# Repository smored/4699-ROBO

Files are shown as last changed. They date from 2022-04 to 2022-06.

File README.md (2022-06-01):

Computer Vision Target Shooting Robot
=====================================

Objective:
----------
"The design project is to develop a robot that competes in an [arena](https://cdn.discordapp.com/attachments/817281300821049352/977007824553009233/unknown.png). The robot begins in a start box, and when driving forward breaks an IR beam to start the timer. The robot must then strike 4 contact plates and continue on to the finish box where the timer is stopped. The arena must be completed in two different modes, 1) teleoperation where the user drives via commands and images over TCP/IP and 2) autonomous mode where the robot solves the arena without human intervention."

Our Solution:
-------------
We decided to base our design around two [NEMA 17](https://www.amazon.ca/gp/product/B09N3NRTW9/ref=ppx_yo_dt_b_asin_title_o06_s01?ie=UTF8&psc=1) stepper motors using respective [L298N](https://www.amazon.ca/gp/product/B00XAGRQTO/ref=ppx_yo_dt_b_asin_title_o07_s00?ie=UTF8&psc=1) driver circuit boards and a [Teensy 4.0](https://www.amazon.ca/Teensy-4-0-with-Pins/dp/B08259KDHY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) to interface the motors to the [Raspbery Pi 4b](https://www.amazon.ca/s?k=rasberry+pi+4+b&crid=1HV9MO5X30TG&sprefix=rasb%2Caps%2C238&ref=nb_sb_ss_ts-doa-p_1_4). We would use two [ultrasonic sensors](https://www.sparkfun.com/products/15569) for positional alignment, a [servo](https://www.amazon.ca/gp/product/B07VJG5QTJ/ref=ppx_yo_dt_b_asin_title_o05_s00?ie=UTF8&psc=1) for turret aiming, a [servo](https://www.amazon.ca/gp/product/B07KR24YX8/ref=ppx_yo_dt_b_asin_title_o03_s00?ie=UTF8&psc=1) for firing at the targets, and finally a [pi camera](https://www.amazon.ca/Keyestudio-Camera-Module-5MP-Raspberry/dp/B073RCXGQS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). We decided to split the main functionality of the robot into two parts: Driving (Teensy) and Detection (Raspberry Pi). There are two main reasons for this decision, first we wanted to unload as much possible processing from the raspberry pi so that our computer vision algorithm could run faster, and second it allowed us to completely isolate our workloads into two seperate entities, and thus we could work asychronously. 

For Auto mode our algorithm was based around a state machine, each state being defined as a portion of the arena. The Teensy would drive the motors to the first location, wait for feedback from the Pi on when the target was successfully hit, then move to the second target, and so on. The Pi would grab the state of each target from a server hosted by the arena over TCP/IP, and pass that information onto the Teensy via UART. 

The method used to aim the cannon was to use the pi camera to scan for ArUCO QR codes, using that information encoded into screenspace, determine whether the target was on the left or right of the centre of the camera. If the ArUCO was in the centre, it would fire the cannon.

In manual driving mode, the user would input keypresses into a windows client on a laptop that communicated with the Pi over TCP/IP. The client additionally fetched a camera feed from the arena, and a camera feed from the Pi to enable the user to fully drive the unit without line of sight to the arena.

Media:
------
PCB pic
robot pic 1
servo pic

[More Robot](https://photos.app.goo.gl/skK17sW5vWhY1REk8)

Credits:
-------
**Kurt Querengesser**

Author of PI code and Lead Parts Designer

Kurt Querengesser (https://www.linkedin.com/in/kurt-querengesser/)

**Michael Andrews**

Author of Microcontroller Code and Lead PCB Designer

Michael Andrews (https://www.linkedin.com/in/michael-andrews-b0ab8217a/)

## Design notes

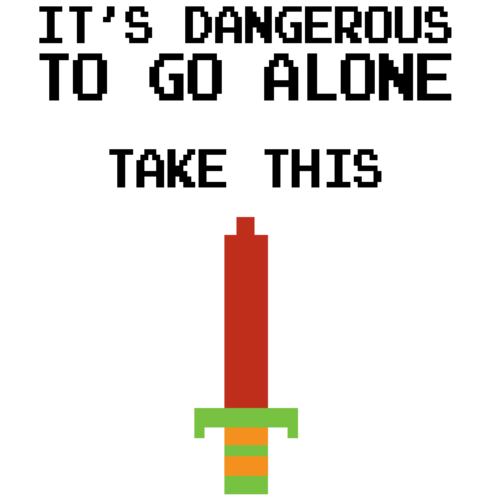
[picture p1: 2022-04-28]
KiCad PiHat/Graphics/Dangerous.png

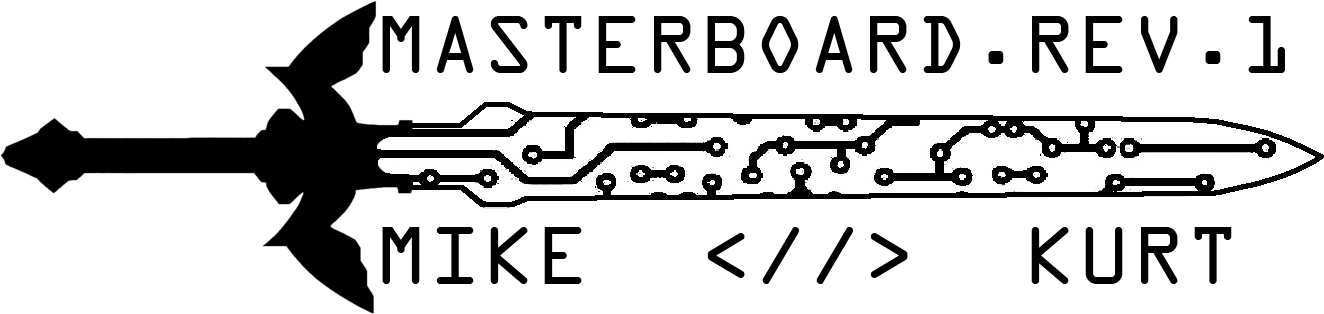
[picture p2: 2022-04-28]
KiCad PiHat/Graphics/masterboard.png

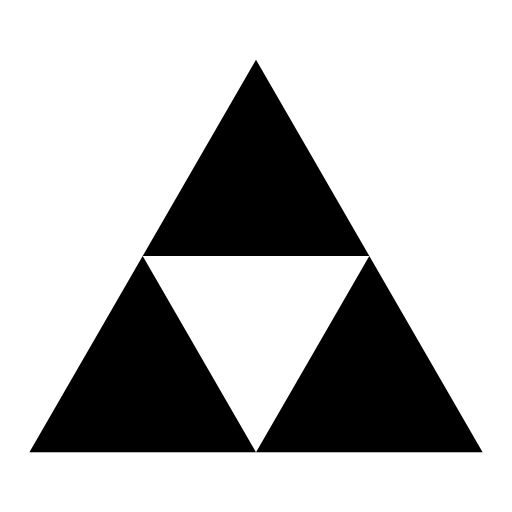
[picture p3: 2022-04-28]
KiCad PiHat/Graphics/Triforce.png

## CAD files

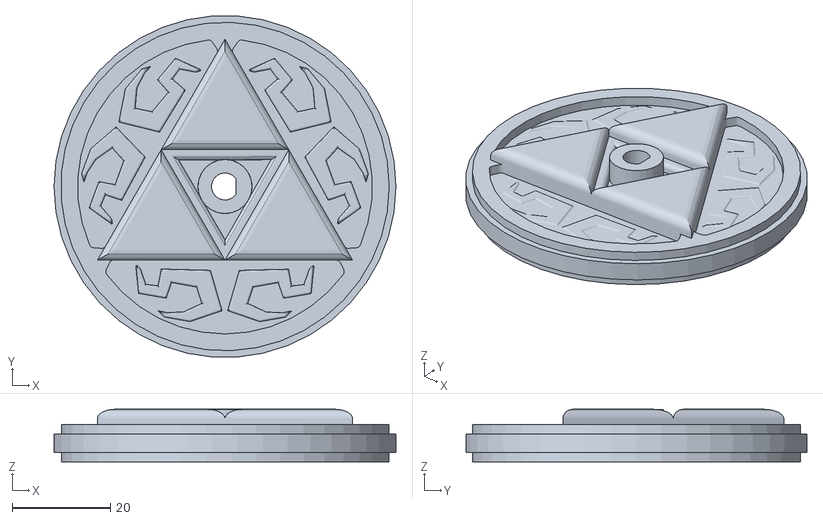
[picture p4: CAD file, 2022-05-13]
MODELS/STLs/wheel.stl
69.6 x 69.4 x 10.7

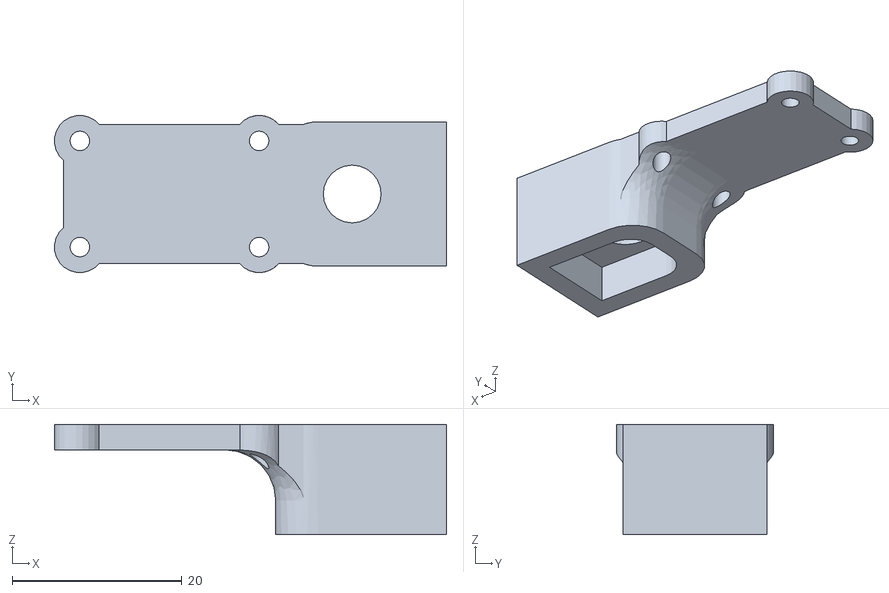
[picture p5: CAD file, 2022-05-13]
MODELS/STLs/camera_mount.stl
46.1 x 18.5 x 13.0

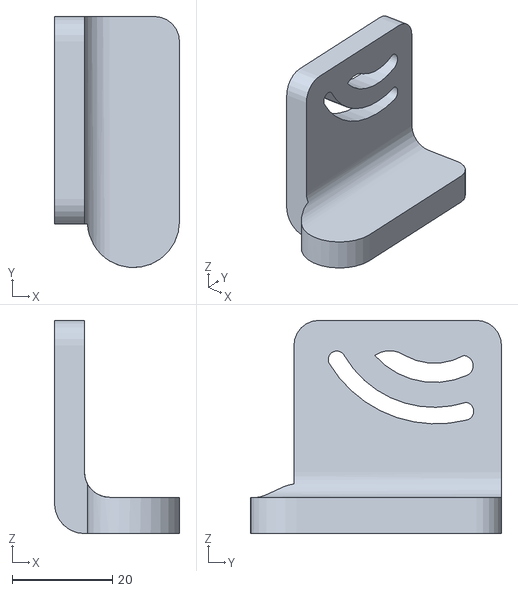
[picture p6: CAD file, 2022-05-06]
MODELS/STLs/launcher_mount.stl
24.9 x 50.0 x 42.5

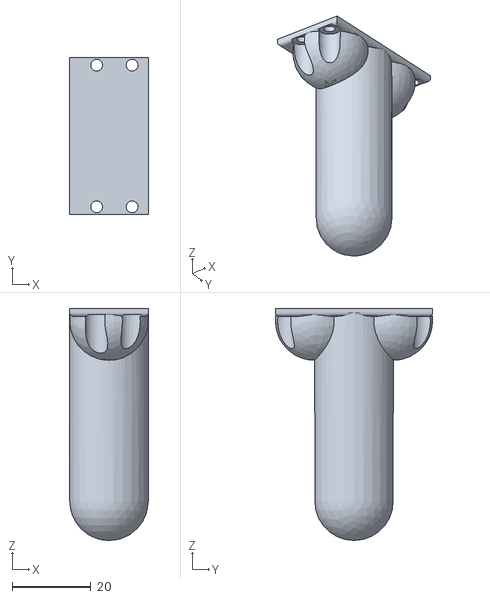
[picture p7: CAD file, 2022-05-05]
MODELS/STLs/C&B.stl
20.0 x 40.0 x 58.9

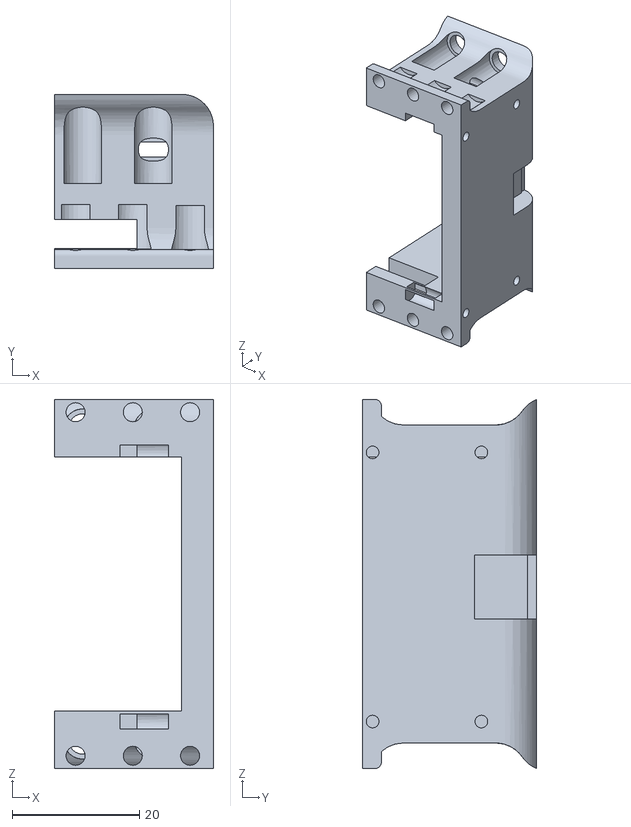
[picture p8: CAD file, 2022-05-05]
MODELS/STLs/servo_mount.stl
25.0 x 27.4 x 58.0

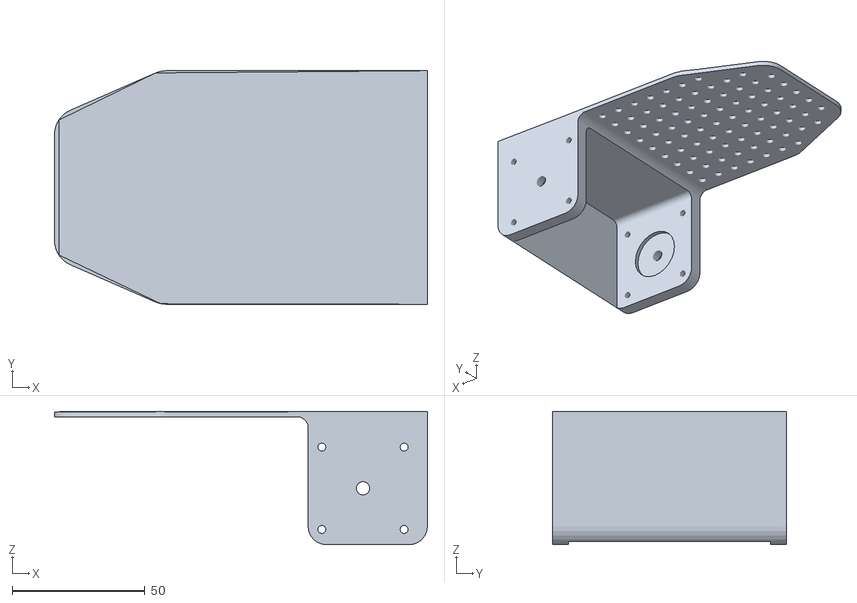
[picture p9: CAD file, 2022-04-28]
MODELS/STLs/chassis.stl
140.5 x 88.0 x 50.3

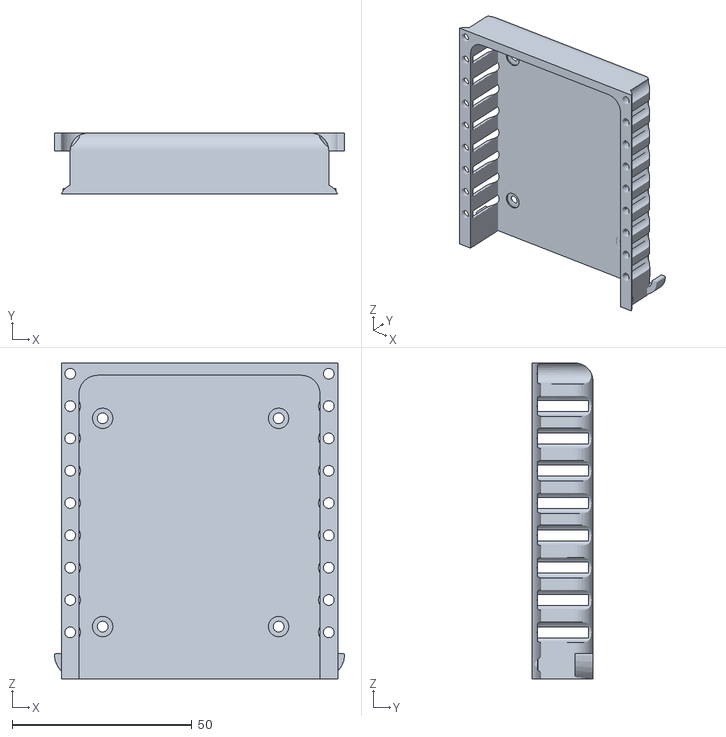
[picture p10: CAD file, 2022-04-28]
MODELS/STLs/battery_holder.stl
80.9 x 17.0 x 88.0

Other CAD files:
MODELS/CarBase.DWG
MODELS/RaspberryHatBoard.DWG
MODELS/launcher.DWG
MODELS/wheel.dwg

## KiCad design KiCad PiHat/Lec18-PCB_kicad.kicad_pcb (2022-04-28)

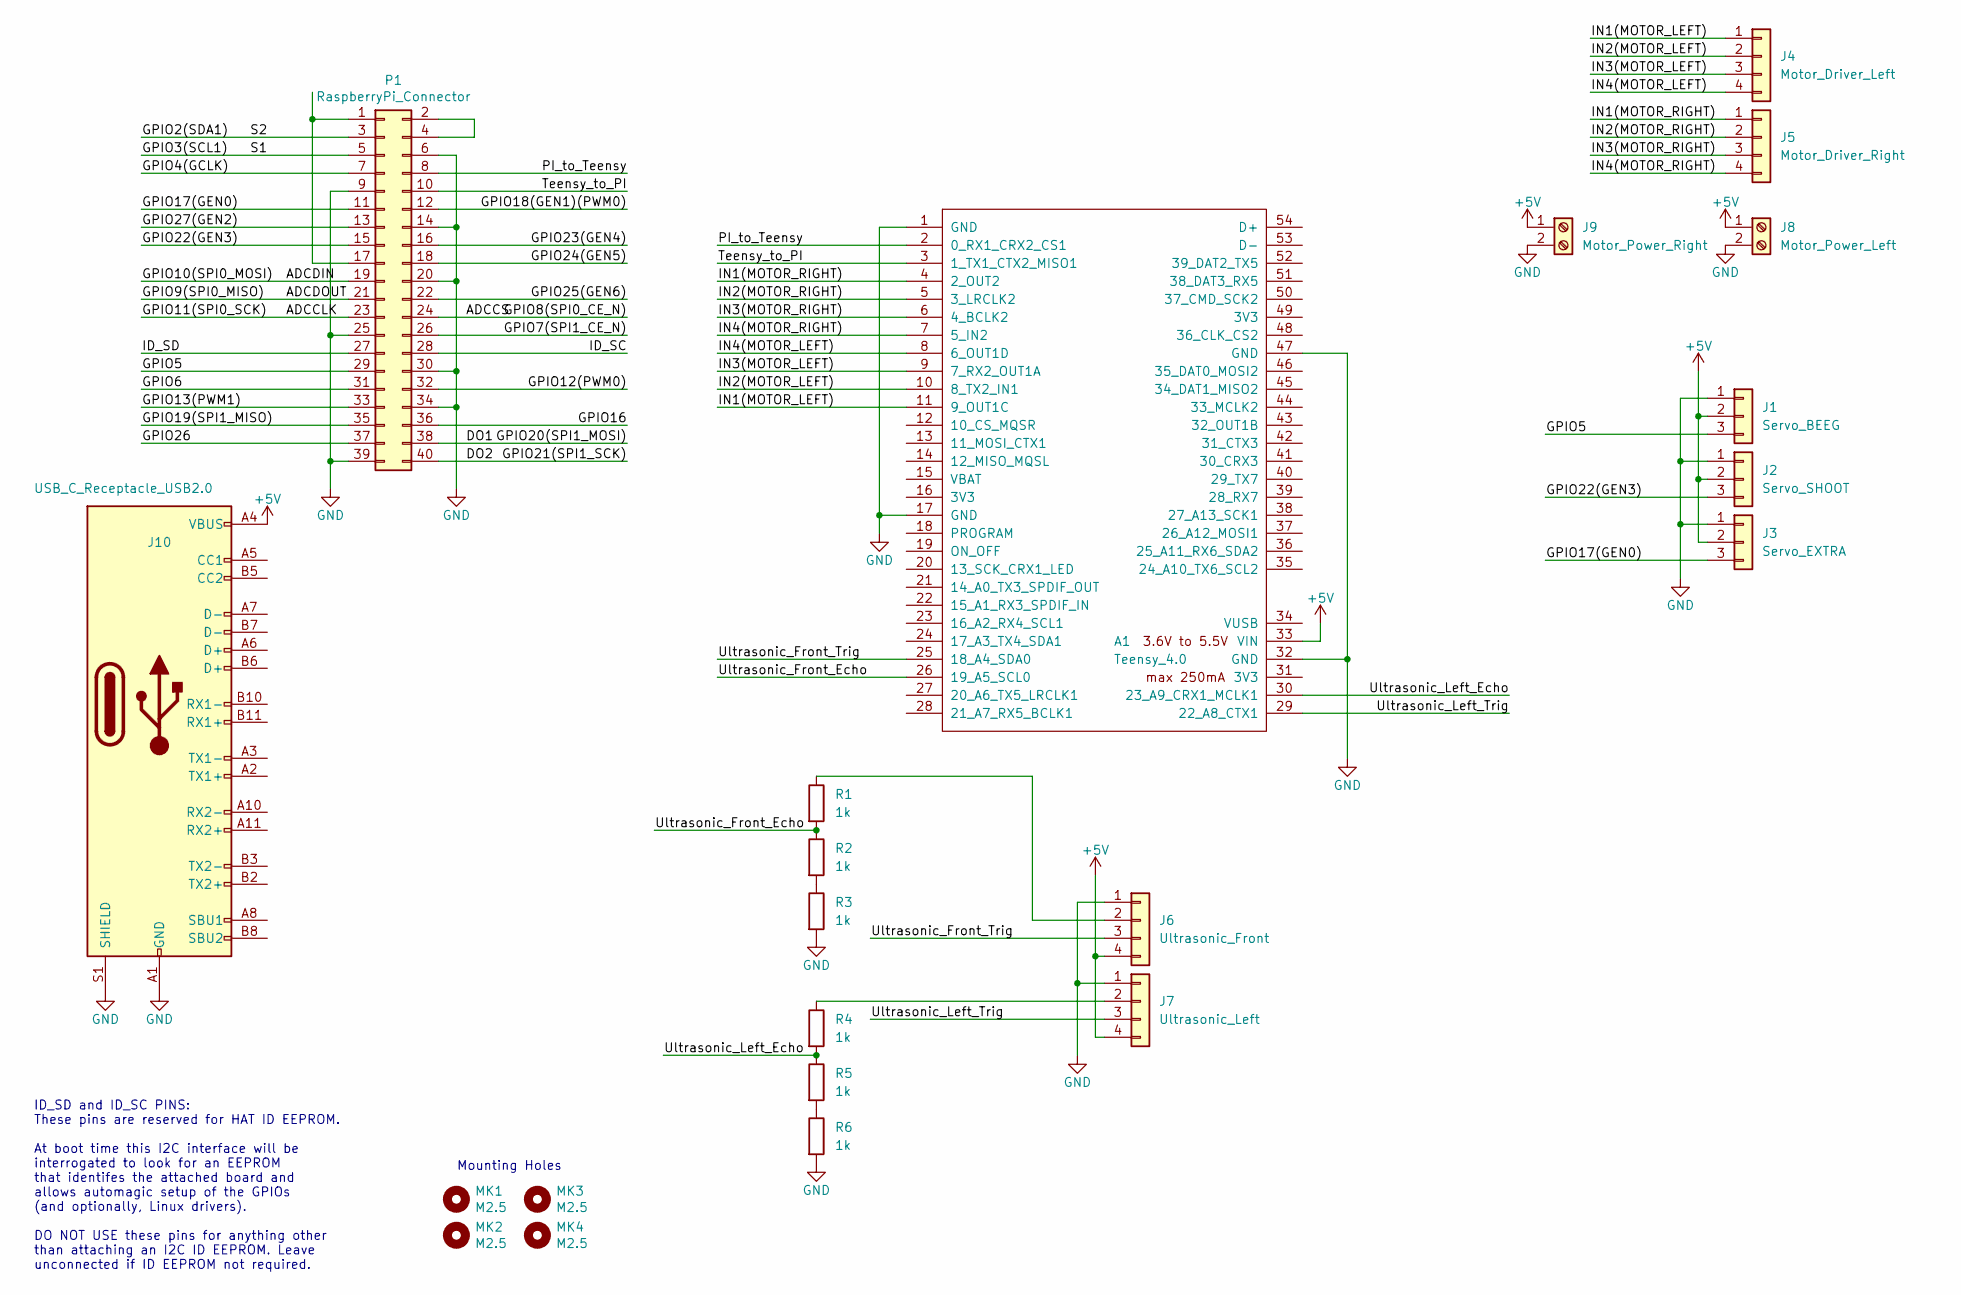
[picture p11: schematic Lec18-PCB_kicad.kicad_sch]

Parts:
A1: Teensy_4.0; Teensy40
J1: Servo_BEEG; PinSocket_1x03_P2.54mm_Vertical
J2: Servo_SHOOT; PinSocket_1x03_P2.54mm_Vertical
J3: Servo_EXTRA; PinSocket_1x03_P2.54mm_Vertical
J4: Motor_Driver_Left; PinSocket_1x04_P2.54mm_Vertical
J5: Motor_Driver_Right; PinSocket_1x04_P2.54mm_Vertical
J6: Ultrasonic_Front; PinSocket_1x04_P2.54mm_Vertical
J7: Ultrasonic_Left; PinSocket_1x04_P2.54mm_Vertical
J8: Motor_Power_Left; TerminalBlock_bornier-2_P5.08mm
J9: Motor_Power_Right; TerminalBlock_bornier-2_P5.08mm
J10: USB_C_Receptacle_USB2.0; USB_C_Receptacle_GCT_USB4085
MK1, MK2, MK3, MK4: M2.5; MountingHole_2.7mm_M2.5
P1: RaspberryPi_Connector; PinSocket_2x20_P2.54mm_Vertical
R1, R2, R3, R4, R5, R6: 1k; R_Axial_DIN0207_L6.3mm_D2.5mm_P7.62mm_Horizontal

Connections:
+5V: A1.33 (VIN), J1.2, J2.2, J3.2, J6.4, J7.4, J8.1, J9.1, J10.A4 (VBUS), J10.A9 (VBUS), J10.B4 (VBUS), J10.B9 (VBUS)
/ADCCLK: P1.23
/ADCCS: P1.24
/ADCDIN: P1.19
/ADCDOUT: P1.21
/DO1: P1.38
/DO2: P1.40
/GPIO2(SDA1): P1.3
/GPIO3(SCL1): P1.5
/GPIO4(GCLK): P1.7
/GPIO5: J1.3, P1.29
/GPIO6: P1.31
/GPIO7(SPI1_CE_N): P1.26
/GPIO12(PWM0): P1.32
/GPIO13(PWM1): P1.33
/GPIO16: P1.36
/GPIO17(GEN0): J3.3, P1.11
/GPIO18(GEN1)(PWM0): P1.12
/GPIO19(SPI1_MISO): P1.35
/GPIO22(GEN3): J2.3, P1.15
/GPIO23(GEN4): P1.16
/GPIO24(GEN5): P1.18
/GPIO25(GEN6): P1.22
/GPIO26: P1.37
/GPIO27(GEN2): P1.13
/ID_SC: P1.28
/ID_SD: P1.27
/IN1(MOTOR_LEFT): A1.11 (9_OUT1C), J4.1
/IN1(MOTOR_RIGHT): A1.4 (2_OUT2), J5.1
/IN2(MOTOR_LEFT): A1.10 (8_TX2_IN1), J4.2
/IN2(MOTOR_RIGHT): A1.5 (3_LRCLK2), J5.2
/IN3(MOTOR_LEFT): A1.9 (7_RX2_OUT1A), J4.3
/IN3(MOTOR_RIGHT): A1.6 (4_BCLK2), J5.3
/IN4(MOTOR_LEFT): A1.8 (6_OUT1D), J4.4
/IN4(MOTOR_RIGHT): A1.7 (5_IN2), J5.4
/PI_to_Teensy: A1.2 (0_RX1_CRX2_CS1), P1.8
/Teensy_to_PI: A1.3 (1_TX1_CTX2_MISO1), P1.10
/Ultrasonic_Front_Echo: A1.26 (19_A5_SCL0), R1.2, R2.1
/Ultrasonic_Front_Trig: A1.25 (18_A4_SDA0), J6.3
/Ultrasonic_Left_Echo: A1.30 (23_A9_CRX1_MCLK1), R4.2, R5.1
/Ultrasonic_Left_Trig: A1.29 (22_A8_CTX1), J7.3
GND: A1.1 (GND), A1.17 (GND), A1.32 (GND), A1.47 (GND), J1.1, J2.1, J3.1, J6.1, J7.1, J8.2, J9.2, J10.A1 (GND), J10.A12 (GND), J10.B1 (GND), J10.B12 (GND), J10.S1 (SHIELD), P1.6, P1.9, P1.14, P1.20, P1.25, P1.30, P1.34, P1.39, R3.2, R6.2
unnamed: J7.2, R4.1
unnamed: P1.1, P1.17
unnamed: P1.2, P1.4
unnamed: J6.2, R1.1
unnamed: R2.2, R3.1
unnamed: R5.2, R6.1

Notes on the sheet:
Mounting Holes
ID_SD and ID_SC PINS: These pins are reserved for HAT ID EEPROM. At boot time this I2C interface will be interrogated to look for an EEPROM that identifes the attached board and allows automagic setup of the GPIOs (and optionally, Linux drivers). DO NOT USE these pins for anything other than attach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

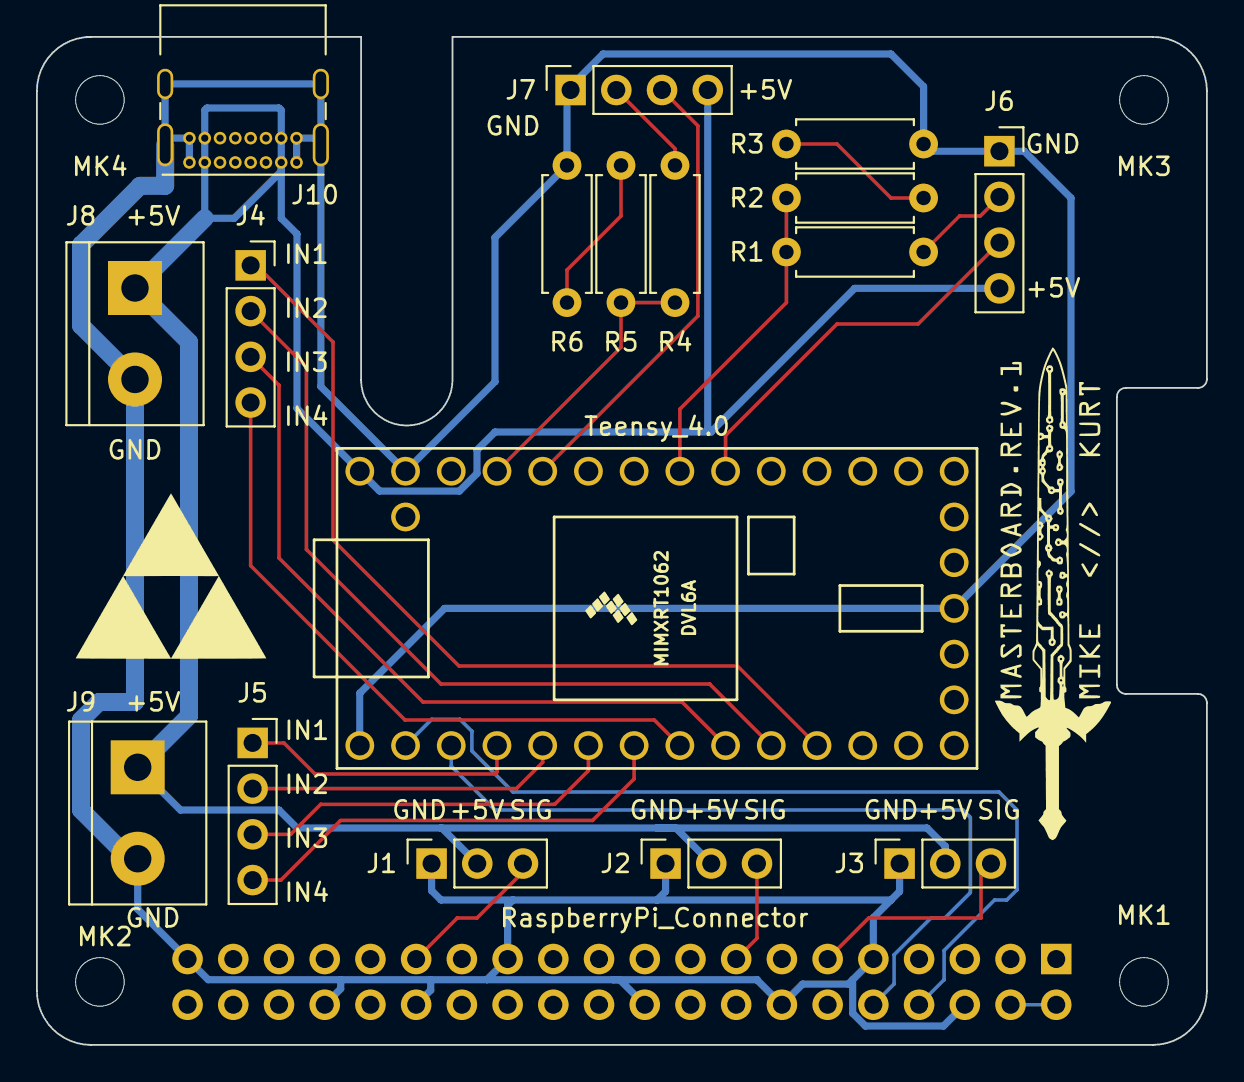
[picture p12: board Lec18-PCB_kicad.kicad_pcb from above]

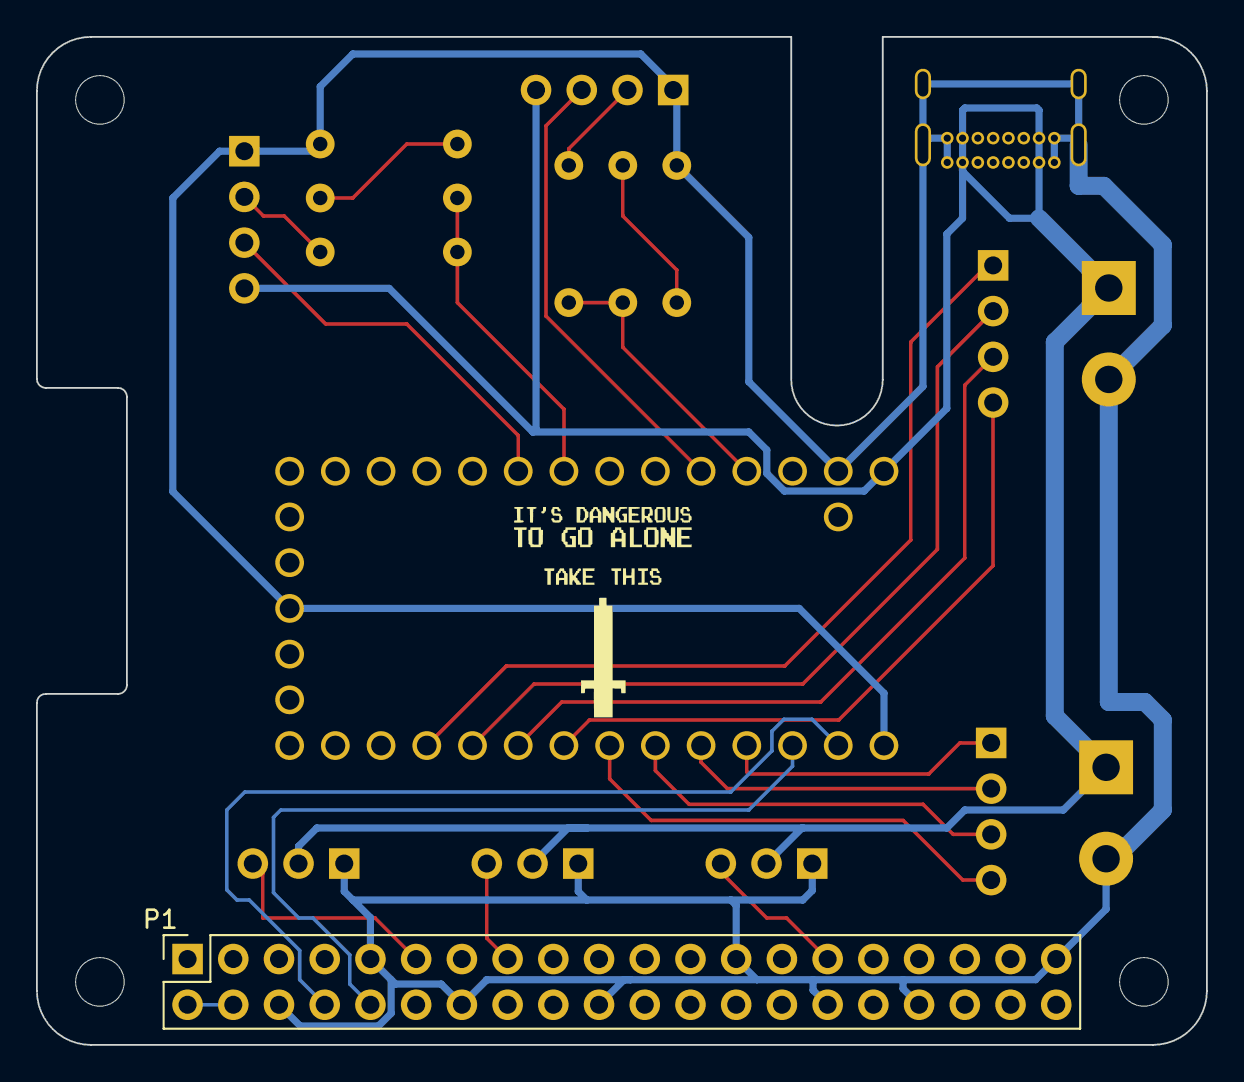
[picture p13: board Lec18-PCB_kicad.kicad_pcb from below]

Board: 2 copper layers, 65.0 x 56.0 mm, 25 parts (2 on the bottom side), 25 nets.

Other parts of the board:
Logo: LOGO; Masterboard_Logo
Triforce: LOGO; Triforce
image: LOGO; Dangerous

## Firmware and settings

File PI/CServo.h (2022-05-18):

#pragma once
#include <pigpio.h>
#include <iostream>
#include <thread>

#define DEFAULT_SPEED 10
#define DEFAULT_DELAY 50
//#define DEFAULT_POS 2500

/** CServo.h
 *
 * @brief Servo Class for holding data
 *
 * @author Kurt Querengesser
 *
 * @version 1.0 -- 09 May 2022
 */
class CServo {
private:
    int _gpioPin;
    int _pos;
    int _speed;
    int _delay;
    const int DEFAULT_POS;
    //int _lastPos;
public:

    // Default constructor
    CServo(int gpio, int speed = DEFAULT_SPEED, int delay = DEFAULT_DELAY, int startpos = 2500) : DEFAULT_POS(startpos) {
        _gpioPin = gpio;
        _pos = startpos;
       // _lastPos = _pos;
        _speed = speed;
        _delay = delay;
      }

    ~CServo() {;}

    const int middle = 1500; ///< middle position of servo
    const int left = 2500; ///< left position of servo
    const int right = 500; ///< right position of servo

    /**
    * @brief setter for speed
    */
    void setSpeed(int speed) { this->_speed = speed; }

    /**
    * @brief setter for delay
    */
    void setDelay(int delay) { if (delay > 0) this->_delay = delay; }

    /**
    * @brief getter for speed
    */
    int getSpeed() { return this->_speed; }

    /**
    * @brief getter for delay
    */
    int getDelay() { return this->_delay; }

    /**
    * @brief Method used for repositioning the servo. adds or subtracts the speed from the desired position Does not move the servo head. Call moveServo() to update head position
    * @param positive: whether to add or subtract speed value
    */
    void add(bool positive) {
        int pos = _pos;
        if (positive) pos += _speed;
        if (!positive) pos -= _speed;
        if (pos > left) pos = left;
        if (pos < right) pos = right;
        this->_pos = pos;
    }

    /**
    * @brief Method used for setting the servo position absolutely. Call moveServo() to update head position
    * @param pos: position to move to in milliseconds (500 - 2500)
    */
    void setPos(int pos) {
        if (pos > left) pos = left;
        if (pos < right) pos = right;
        this->_pos = pos;
    }

    /**
    * @brief Updates the position of the servo head
    */
    void moveServo() {
        gpioServo(_gpioPin, _pos);
    }


    /**
    * @brief returns the servo to the default position
    */
    void resetServo() {_pos = DEFAULT_POS; moveServo(); std::this_thread::sleep_for(std::chrono::milliseconds(500)); }
};

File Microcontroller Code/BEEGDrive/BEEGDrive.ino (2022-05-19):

#include <AccelStepper.h>
#include "BEEGDrive.h"

enum mode { AUTO, MANUAL, NONE };
enum automaticMode { startWait, target1, target2, target3, target4, finishAUTO };
enum movementState { forward, turn, forward_second, turn_complete };


String input = "NULL";

mode bigMode;
automaticMode autoMode;
movementState target2State;
movementState target3State;

// initialize the stepper library on pins 8 through 11:
AccelStepper leftMotor(AccelStepper::FULL4WIRE, IN1_Left, IN2_Left, IN3_Left, IN4_Left);
AccelStepper rightMotor(AccelStepper::FULL4WIRE, IN1_Right, IN2_Right, IN3_Right, IN4_Right);

void setup() {
    //Set motor max speed and desired acceleration
    leftMotor.setMaxSpeed(1000);
    rightMotor.setMaxSpeed(1000);
    leftMotor.setAcceleration(200);
    rightMotor.setAcceleration(200);
    leftMotor.setPinsInverted(true, true, false);
    rightMotor.setPinsInverted(true, true, false);
    // initialize the serial port:
    Serial.begin(9600);
    Serial1.begin(9600);
    bigMode = MANUAL;
    pinMode(2, INPUT);
    pinMode (LED_BUILTIN, OUTPUT);
    pinMode(20, INPUT_PULLDOWN);
    pinMode(19, INPUT_PULLDOWN);
    pinMode(18, INPUT_PULLDOWN);
    pinMode(17, INPUT_PULLDOWN);
}

void loop() {

    //State Machine (Overlord)
    switch(bigMode){
        //State Machine (Auto)
        case AUTO:
                Serial.print("AUTO defaulted");
                switch(autoMode){
                //State 0
                case startWait:
                    //Wait for start command
                    //Go to next state when start command is received
                    readPI(input);
                    if(input == STOPCMD){
                        stopDriving();
                    }
                    else if(input == STARTCMD){
                        digitalWrite(LED_BUILTIN, HIGH);
                        delay(250);
                        digitalWrite(LED_BUILTIN, LOW);
                        autoMode = target1;
                        input = "";
                        leftMotor.moveTo(380);
                        rightMotor.moveTo(380);
                        target2State = forward;
                        target3State = forward;
                    }
                    break;
                //State 1
                case target1:
                    //Drive forward approx 2 ft (554 steps per motor)
                    //Wait to receive confirmation that Target 1 has been hit
                    //Goes to next state upon receiving the confirmation from PI
                    readPI(input);
                    if(input == STOPCMD){
                        stopDriving();
                    }
                    else if (leftMotor.distanceToGo() != 0 && rightMotor.distanceToGo() != 0){
                        leftMotor.run();
                        rightMotor.run();
                    }
                    else if(input == TARGET1){
                        autoMode = target2;
                        input = "";
                        leftMotor.setCurrentPosition(0);
                        rightMotor.setCurrentPosition(0);
                        leftMotor.moveTo(400);
                        rightMotor.moveTo(400);
                    }
                    break;
                
                //State 2
                case target2:
                    //Sweeping turn to be in front of Target 2
                    //Wait to receive confirmation that Target 2 has been hit
                    //Goes to next state upon receiving the confirmation from PI
                    //Drive forward approx 2 ft (554 steps per motor)
                    //Wait to receive confirmation that Target 1 has been hit
                    //Goes to next state upon receiving the confirmation from PI
                    readPI(input);
                    if(input == STOPCMD){
                        stopDriving();
                    }
                    else if(target2State != turn_complete){
                        moveToTarget(target2State);
                    }
                    else if(input == TARGET2){
                        autoMode = target3;
                        input = "";
                        leftMotor.setCurrentPosition(0);
                        rightMotor.setCurrentPosition(0);
                        leftMotor.moveTo(370);
                        rightMotor.moveTo(370);
                    }
                    break;
                //State 3
                case target3:
                    //Sweeping turn to be in front of Target 3
                    //Wait to receive confirmation that Target 3 has been hit
                    //Goes to next state upon receiving the confirmation from PI
                    readPI(input);
                    if(input == STOPCMD){
                        stopDriving();
                    }
                    else if(target3State != turn_complete){
                        moveToTarget(target3State);
                    }
                    else if(input == TARGET3){
                        autoMode = target4;
                        input = "";
                        leftMotor.setCurrentPosition(0);
                        rightMotor.setCurrentPosition(0);
                        leftMotor.moveTo(95);
                    }
                    break;
                //State 4 
                case target4:
                    //Spin 45 degrees and move forward to be in front of the 4th target
                    readPI(input);
                    if(input == STOPCMD){
                        stopDriving();
                    }
                    else if(rightMotor.currentPosition() == 0 && leftMotor.currentPosition() == 86){
                        rightMotor.setCurrentPosition(0);
                        leftMotor.setCurrentPosition(0);
                        rightMotor.moveTo(500);
                        leftMotor.moveTo(500);
                        delay(250);
                    }
                    else if(rightMotor.distanceToGo() != 0 || leftMotor.distanceToGo() != 0){
                      leftMotor.run();
                      rightMotor.run();
                    }
                    else if(input == TARGET4){
                        autoMode = finishAUTO;
                        input = "";
                        rightMotor.setCurrentPosition(0);
                        leftMotor.setCurrentPosition(0);
                        leftMotor.moveTo(-560);
                        rightMotor.moveTo(-560);
                    }
                    
                    //Wait to receive confirmation that Target 4 has been hit
                    //Goes to next state upon receiving the confirmation from PI
                    break;
                //State 5 (Close Shot)
                //case target4:
                    //Drive to front of 4th target
                    //Wait to receive confirmation that Target 4 has been hit
                    //Goes to next state upon receiving the confirmation from PI
                    //break;
                //State 6 (Close Shot)
                case finishAUTO:
                    //Turn 180 degrees
                    //Drive forward forward_second to area of target 3
                    //Turn to face end zone
                    //Drive forward into end zone
                    readPI(input);
                    if(input == STOPCMD){
                        stopDriving();
                    }
                    else if(rightMotor.currentPosition() == 0 && leftMotor.currentPosition() == -77 && leftMotor.distanceToGo() == 0){
                        delay(250);
                        rightMotor.setCurrentPosition(0);
                        leftMotor.setCurrentPosition(0);
                        rightMotor.moveTo(615);
                        leftMotor.moveTo(615);
                    }
                    else if(leftMotor.distanceToGo() == 0 && rightMotor.currentPosition() == -560){
                        delay(250);
                        rightMotor.setCurrentPosition(0);
                        leftMotor.setCurrentPosition(0);
                        leftMotor.moveTo(-77);
                    }
                    else{
                      leftMotor.run();
                      rightMotor.run();
                    }
                }
        break;
        
    case MANUAL:
        while(digitalRead(FORWARD_PIN)){
          rightMotor.setSpeed(MANUAL_SPEED);
          leftMotor.setSpeed(MANUAL_SPEED);
          rightMotor.move(100);
          leftMotor.move(100);
          rightMotor.runSpeed();
          leftMotor.runSpeed();
        }
        while(digitalRead(RIGHT_PIN)){
          leftMotor.setSpeed(MANUAL_SPEED/2);
          leftMotor.move(100);
          leftMotor.runSpeed();
        }
        while(digitalRead(LEFT_PIN)){
          rightMotor.setSpeed(MANUAL_SPEED/2);
          rightMotor.move(100);
          rightMotor.runSpeed();
        }
        while(digitalRead(BACK_PIN)){
          rightMotor.move(-100);
          leftMotor.move(-100);
          rightMotor.setSpeed(-MANUAL_SPEED);
          leftMotor.setSpeed(-MANUAL_SPEED);
          rightMotor.runSpeed();
          leftMotor.runSpeed();
        }
        break;
    case NONE:
        readPI(input);
        if(input == AUTOCMD){
          bigMode = AUTO;
          autoMode = startWait;
          Serial.print("BigMode is AUTO");
        }
        else if(input == MANUALCMD){
          bigMode = MANUAL;
          Serial.print("BigMode is MANUAL\n\n");
        }
        else{
          bigMode = NONE;
        }
        break;
    }
}

void readPI(String &input){
    if (Serial1.available() > 0){
        input = Serial1.readStringUntil('\n');
        Serial.print("R PI sent: ");
        Serial.print(input);
        Serial.print("\n");
    }
}

void moveToTarget(movementState &state){
  switch(state){
      case forward:
          if(leftMotor.distanceToGo() == 0 && rightMotor.distanceToGo() == 0){
              leftMotor.setCurrentPosition(0);
              rightMotor.setCurrentPosition(0);
              leftMotor.moveTo(145);
              state = turn;
              delay(250);
          }
          else{
              leftMotor.run();
              rightMotor.run();
          }
          break;
          case turn:
              if(leftMotor.distanceToGo() == 0 && rightMotor.distanceToGo() == 0){
                  leftMotor.setCurrentPosition(0);
                  rightMotor.setCurrentPosition(0);
                  leftMotor.moveTo(290);
                  rightMotor.moveTo(290);
                  state = forward_second;
                  delay(250);
             }
             else{
                 leftMotor.run();
                 rightMotor.run();
             }
             break;
             case forward_second:
             if(leftMotor.distanceToGo() == 0 && rightMotor.distanceToGo() == 0){
                state = turn_complete;
             }
             else{
                leftMotor.run();
                rightMotor.run();
             }
             break;
    }
}

void stopDriving(){
    bigMode = NONE;
    input = "";
    leftMotor.setCurrentPosition(0);
    rightMotor.setCurrentPosition(0);
    leftMotor.moveTo(0);
    rightMotor.moveTo(0);
    autoMode = startWait;
}

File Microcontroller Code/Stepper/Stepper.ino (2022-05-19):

#include <Stepper.h>

#define TARGET1   1
#define TARGET2   2
#define TARGET3   3
#define TARGET4   4
#define STARTCMD  "START"
#define STOPCMD   "STOP"
#define AUTOCMD   "AUTO"
#define MANUALCMD "MANUAL"

const int stepsPerRevolution = 200;

enum mode { AUTO, MANUAL, NONE };
enum automaticMode { startWait, target1, target2, target3, target4, finish};
mode bigMode = MANUAL;
automaticMode autoMode = startWait;

// initialize the stepper library on pins 8 through 11:
Stepper myStepperLeft(stepsPerRevolution, 8, 9, 10, 11);
Stepper myStepperRight(stepsPerRevolution, 4, 5, 6, 7);

void setup() {
  // set the initial speed at 20 rpm:
  myStepperRight.setSpeed(20);
  myStepperLeft.setSpeed(20);
  // initialize the serial port:
  Serial.begin(9600);
}

void loop() {
  drive(2000, 2000, 60);
  delay(2000);

  /*String input;

  //State Machine (Overlord)
  switch(bigMode){
    //State Machine (Auto)
    case AUTO:

      while(bigMode == AUTO){

        switch(autoMode){
          //State 0
          case startWait:
            //Wait for start command
            //Go to next state when start command is received
            input = readPI();
            if(input == STARTCMD){
              autoMode = target1;
              input = "";
            }
            else if(input == STOPCMD){
              bigMode = NONE;
            }
          
          //State 1
          case target1:
            //Drive forward approx 2 ft (554 steps per motor)
            //Wait to receive confirmation that Target 1 has been hit
            //Goes to next state upon receiving the confirmation from PI
            drive(554, 554, 60);
            input = readPI();
            if(input == STARTCMD){
              autoMode = target1;
            }
            else if(input == STOPCMD){
              bigMode = NONE;
            }

          //State 2
          //case target2:
            //Sweeping turn to be in front of Target 2
            //Wait to receive confirmation that Target 2 has been hit
            //Goes to next state upon receiving the confirmation from PI

          //State 3
          //case target3:
            //Sweeping turn to be in front of Target 3
            //Wait to receive confirmation that Target 3 has been hit
            //Goes to next state upon receiving the confirmation from PI

          //State 4 (Long Shot)
          //case target4:
            //Wait to receive confirmation that Target 4 has been hit
            //Goes to next state upon receiving the confirmation from PI

          //State 4 (Close Shot)
          //case target4:
            //Drive to front of 4th target
            //Wait to receive confirmation that Target 4 has been hit
            //Goes to next state upon receiving the confirmation from PI

          //State 5 (Long Shot)
          //case finish:
            //Drive forward into end zone

          //State 5 (Close Shot)
          //case finish:
            //Turn 180 degrees
            //Drive forward back to area of target 3
            //Turn to face end zone
            //Drive forward into end zone
        }
      }
      break;
    case MANUAL:
    //State Machine (Manual)
      drive(200, 200, 60);
      delay(5000);
      break;
    default:
      if(readPI() == AUTOCMD){
        bigMode = AUTO;
        //autoMode = 
      }
      else if (readPI() == MANUALCMD){
        bigMode = MANUAL;
      }
      else{
        bigMode = MANUAL;
      }
    break;
  }
  /*drive(2000, 1000, 100);
  delay(2000);*/
}

void drive(int rightSteps, int leftSteps, int rpm){

  //Set the RPM's of the motors to be 
  float ratio;
  float rightRPM;
  float leftRPM;
  if(rightSteps > leftSteps){
    ratio = abs(float(rightSteps)/float(leftSteps));
    rightRPM = rpm*ratio;
    leftRPM = rpm;
  }
  else if(leftSteps > rightSteps){
    ratio = abs(float(leftSteps)/float(rightSteps));
    rightRPM = rpm;
    leftRPM = rpm*ratio;
  }
  else{
    rightRPM = rpm;
    leftRPM = rpm;
  }

  int leftCoef = leftSteps/abs(leftSteps);
  int rightCoef = rightSteps/abs(rightSteps);
  
  /*Serial.print("Right:");
  Serial.print(rightSteps);
  Serial.print(" Left:");
  Serial.print(leftSteps);
  Serial.print(" Ratio:");
  Serial.print(ratio);
  Serial.print(" Right RPM:");
  Serial.print(rightRPM);
  Serial.print(" Left RPM:");
  Serial.print(leftRPM);*/

  int rightStepsDone = 0;
  int leftStepsDone = 0;

  myStepperRight.setSpeed(rightRPM);
  myStepperLeft.setSpeed(leftRPM);
  for(int x = 0; x < abs(leftSteps) && x < abs(rightSteps); x++){
    if(rightSteps > leftSteps){
      myStepperRight.step(rightCoef*ratio);
      myStepperLeft.step(leftCoef);
      rightStepsDone += ratio;
      leftStepsDone++;
    }
    else if(leftSteps > rightSteps){
      myStepperRight.step(rightCoef);
      myStepperLeft.step(leftCoef*ratio);
      leftStepsDone += ratio;
      rightStepsDone++;
    }
    else{
      myStepperRight.step(1);
      myStepperLeft.step(1);
      rightStepsDone++;
      leftStepsDone++;
    }
  }
  /*Serial.print(" Right Steps Done:");
  Serial.print(rightStepsDone);
  Serial.print(" Left Steps Done:");
  Serial.print(leftStepsDone);
  Serial.print('\n');*/
}

String readPI(){
  if(Serial.available() > 0){
    String data = Serial.readStringUntil('\n');
    Serial.println(data);
    return data;
  }
  return "NULL";
}

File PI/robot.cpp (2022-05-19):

#include "robot.h"
#include "cvui.h"

robot::robot() {
    // Initialize variables
    _dictionary = cv::aruco::getPredefinedDictionary(cv::aruco::DICT_6X6_250);
    centreDefault();
    _statemap[NULL_STATE] = "NULL";
    _statemap[FIND_T1] = "NULL";
    _statemap[FIND_T2] = "ONE";
    _statemap[FIND_T3] = "TWO";
    _statemap[FIND_T4] = "THREE";
    _statemap[DONE] =    "FOUR";

    _targetmap[NULL_STATE] = TARGET1;
    _targetmap[FIND_T1] = TARGET1; // based on the commands sent from client
    _targetmap[FIND_T2] = TARGET2; // 0 = stop, 1 = find target 1, 2 = find target 2, etc. 5 = done
    _targetmap[FIND_T3] = TARGET3;
    _targetmap[FIND_T4] = TARGET4;
    _targetmap[DONE] = TARGET5;

    _shots = MAX_SHOTS;

    // Initialize states and targets
    //_currentState = STATE::FIND_T1;
    //_targetID = ARUCOIDS::TARGET1;

    // Initialize pigpio
    robot::initPigpio();
    gpioSetMode(PINS::LED, PI_OUTPUT);
    gpioSetMode(PINS::BUTTON, PI_INPUT);
    gpioSetPullUpDown(PINS::BUTTON, PI_PUD_UP); // pullup resistor on button
    _turretServo.resetServo();
    _launcherServo.resetServo();
    gpioSetMode(PINS::FWD, PI_OUTPUT);
    gpioSetMode(PINS::LFT, PI_OUTPUT);
    gpioSetMode(PINS::RGT, PI_OUTPUT);
    gpioSetMode(PINS::REV, PI_OUTPUT);

    // Open Serial device
    initSerial();

    // Make settings window
    const cv::Size canvasSize = cv::Size(300*16/9, 300);
    _settings = cv::Mat::zeros(canvasSize, CV_8UC3);
    cv::imshow("SETTINGS", _settings);
    cvui::init("SETTINGS");
}

robot::~robot() {
    serClose(_serialHandle);
    _server.stop();
    _video.release();
    cv::destroyAllWindows();
    gpioTerminate();
}

void robot::runLoop() {
    // Start robot threads
    std::thread t1(&robot::videoFeed, this);
    t1.detach();
    std::thread t2(&robot::aimCannon, this);
    t2.detach();

    // Start server threads
    std::thread t3(&robot::serverReceive, this); // receive commands from client
    t3.detach();
    //std::thread t4(&robot::serverSendIm, this); // send images repeatedly to client
    //t4.detach();
    std::thread t5(&robot::serverThread, this); // run the server thread
    t5.detach();

    // Start ui thread
    std::thread t6(&robot::uiElements, this);
    t6.detach();

    // Only care about states in auto mode
    if (!MANUAL) {

        // hold states until finished
        // STATE 1
        _currentState = FIND_T1;
        std::cout << "STARTING STATE " << _currentState << std::endl;
        _targetID = TARGET1;
        auto lastState = _currentState;
        while (_currentState <= STATE::FIND_T1);

        // STATE 2
        std::cout << "STATE " << lastState << " FINISHED, STARTING STATE " << _currentState << std::endl;
        _targetID = TARGET2;
        sendString("ONE");
        lastState = _currentState;
        while (_currentState <= STATE::FIND_T2);

        // STATE 3
        std::cout << "STATE " << lastState << " FINISHED, STARTING STATE " << _currentState << std::endl;
        _targetID = TARGET3;
        sendString("TWO");
        lastState = _currentState;
        while (_currentState <= STATE::FIND_T3);

        // STATE 4
        std::cout << "STATE " << lastState << " FINISHED, STARTING STATE " << _currentState << std::endl;
        _targetID = TARGET4;
        sendString("THREE");
        // reposition servo here for hitting target 4 b/c its at an odd angle
        _turretServo.resetServo();
        lastState = _currentState;
        while (_currentState <= STATE::FIND_T4);

        // STATE 5
        std::cout << "STATE " << lastState << " FINISHED, STARTING STATE " << _currentState << std::endl;
        _targetID = TARGET5;
        sendString("FOUR");
    } else {
        while(!_thread_exit);
    }

    _thread_exit = true;
    std::this_thread::sleep_for(std::chrono::milliseconds(2500));
}

void robot::videoFeed() {
    std::cout << "attempting video open\n";
    try {
        _video.open(0);
    } catch (std::exception e) {
        std::cerr << "videoFeed() exception at: " << e.what() << std::endl;
    }
    if (_video.isOpened()) {
        std::cout << "video opened\n";
        cv::Mat canvas; // temporary canvas buffer for flipping image
        do {
            _video >> canvas;
            cv::flip(canvas, _canvas, -1);
            //_canvas = canvas;
            if (!_canvas.empty()) {
                std::vector<int> ids;
                std::vector<std::vector<cv::Point2f>> corners;
                cv::aruco::detectMarkers(_canvas, _dictionary, corners, ids);
                if (ids.size() > 0) {
                    //_tracking = true;
                    cv::aruco::drawDetectedMarkers(_canvas, corners, ids);

                    for (int i = 0; i < ids.size(); i++) { // Find centre using rectangle of two points
                        cv::Rect centresquare = cv::Rect(corners.at(i).at(0), corners.at(i).at(2));
                        cv::Point centre = cv::Point(centresquare.x + centresquare.width/2, centresquare.y + centresquare.height/2);

                        // different behaviour based on manual/auto
                        if (!MANUAL) {
                            // store location of centre of ARUCO of interest
                            if (ids.at(i) == _targetID) {
                                _tracking = true;
                                _centre = centre;
                                cv::circle(_canvas, centre, 10, cv::Scalar(255,0,0), 10);
                            } else {
                                // if ID of interest is not found, turn off tracking, so servo doesnt run off
                                _tracking = false;
                            }
                        } else {
                            _tracking = true;
                            _centre = centre;
                            cv::circle(_canvas, centre, 10, cv::Scalar(255,0,0), 10);
                        }
                    }
                } else {
                    // if no IDs are found, turn off tracking, so servo doesnt run off
                    _tracking = false;
                }
            } else {
                std::cerr << "Cavnas Empty!" << std::endl;
            }
            cv::line(_canvas, cv::Point(SCREEN_X/2, 0), cv::Point(SCREEN_X/2, SCREEN_Y), cv::Scalar(0,0,255));
            cv::line(_canvas, cv::Point(0, SCREEN_Y/2), cv::Point(SCREEN_X, SCREEN_Y/2), cv::Scalar(0,0,255));

            cv::line(_canvas, cv::Point(SCREEN_X*(50+_targetThresh)/100, 0), cv::Point(SCREEN_X*(50+_targetThresh)/100, SCREEN_Y), cv::Scalar(0,255,0));
            cv::line(_canvas, cv::Point(SCREEN_X*(50-_targetThresh)/100, 0), cv::Point(SCREEN_X*(50-_targetThresh)/100, SCREEN_Y), cv::Scalar(0,255,0));

            cv::imshow("RGB", _canvas);
            if (_thread_exit) break;
        } while (cv::waitKey(10) != 'q');
    } else {
        std::cerr << "Video Feed not defined!" << std::endl;
    }
    _thread_exit = true;
}
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

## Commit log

2022-04-12 created repo. unfinished chassis model.
2022-04-12 first chassis prototype finished and printing
    mainly just a test to see if i can fit battery and pi in
    [chassis.stl]
2022-04-27 chassis rv2 modelled with accessories
    scaled up the given chassis model to accommodate more board real estate. added ultrasonic sensors and turret module as well as pi hat and motors. not yet finished since some spaces overlap
    [CarBase.DWG, RaspberryHatBoard.DWG, launcher.DWG]
2022-04-27 Add KiCad PiHat Files
    [Lec18-PCB_kicad.kicad_pcb, Lec18-PCB_kicad.kicad_sch, Lec18-PCB_kicad.sch]
2022-04-28 rearranged whole chassis (r3) working on battery holder
2022-04-28 Ongoing work
    Continued work on schematic and PCB
    [Lec18-PCB_kicad.kicad_pcb, Lec18-PCB_kicad.kicad_sch]
2022-04-28 Finished Schematic
    Schematic finished. Sanity check and routing coming next
    [Lec18-PCB_kicad.kicad_pcb, Lec18-PCB_kicad.kicad_sch, Teensy_4.0_Assembly.STEP]
2022-04-28 3 chassis parts finished
    mainboard, battery holder, and servo holder ready for printing
2022-04-28 routing complete
    [Lec18-PCB_kicad.kicad_pcb, Lec18-PCB_kicad.kicad_sch]
2022-04-28 PCB complete with logos and graphics
    PCB work complete. Going to speak with instructor to make sure all parameters are correct before sending out to have the pcb made.
    [Lec18-PCB_kicad.kicad_pcb]
2022-04-28 pushing STLs for printing
    [battery_holder.stl, chassis.stl, servo_mount.stl]
2022-04-28 chassis stiffened and motor mounts improved
    [chassis.stl]
2022-04-28 PCB Finalized
    [Lec18-PCB_kicad-B_Cu.gbl, Lec18-PCB_kicad-B_Mask.gbs, Lec18-PCB_kicad-B_Silkscreen.gbo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]
2022-04-28 File system cleanup
    [Teensy_4.0_Assembly.STEP]
2022-04-28 raft added to chassis
    [chassis.stl]
2022-04-28 rearranged folders
    [battery_holder.3mf, battery_holder.stl, chassis.stl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]
2022-05-03 worked on the ArUco detection code today, wasnt able to get multithreading working and servo control is NYI
2022-05-03 dragger added to chassis
    ;)
    [C&B.stl]
2022-05-03 updated servo mount
    added wire hole
    [servo_mount.stl]
2022-05-04 not sure tbh
    [Lec18-PCB_kicad.kicad_pcb, Lec18-PCB_kicad.kicad_sch]
2022-05-04 basic servo movement left and right working imshow not displaying to screen for some reason but tracking is still working
2022-05-05 basic Proportional control working with servo
2022-05-05 overhauled launcher mount design
    connects the BEEG servo to launcher. includes an adjustable angle jig
    [launcher_mount.stl]
2022-05-06 made first revision of wheel
    [wheel.stl]
2022-05-06 wheel revision 2
    [wheel.dwg, wheel.stl]
2022-05-07 final commit before I attempt PID integration
2022-05-10 imshow() now properly showing to screen, new classes added for communcation and handling servo
2022-05-10 servo instantiation implemented and used for both turret and launcher
2022-05-11 new wheel design
    [wheel.dwg, wheel.stl]
2022-05-11 wheel tweaks
    [wheel.stl, wheelshaft.stl]
2022-05-11 I done it again
    [wheel.stl]
2022-05-12 added cvui settings window for testing, implemented uart prototype serial communication is a WIP but has been started. added some new members, threads moved into runLoop() instead of constructor. bun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
2022-05-13 wheel modified
    [camera_mount.stl, wheel.stl, wheelshaft.stl]
2022-05-15 made serial communication work with teensy also communicates with laptop client which will send state data
2022-05-17 cleaning up repo
    [battery_holder.3mf]
2022-05-18 sub 40 second run achieved with this code reworked state machine and tweaked delays as well as other small changes
    [CServo.h, robot.cpp, robot.h]
2022-05-19 communcating with teensy for manual over gpio
2022-05-19 Final Teensy code done
